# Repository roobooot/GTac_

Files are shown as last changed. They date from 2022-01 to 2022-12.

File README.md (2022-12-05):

# A Biomimetic Design of HeteroGeneous Tactile Sensor (GTac) Providing Normal and Shear Force Feedback

## General Introduction

This repo includes:

<ul>
  <li>the <a href="https://github.com/roobooot/GTac_/tree/main/software">code</a> 
    <ul>
      <li><a href="https://github.com/roobooot/GTac_/tree/main/software/arduino_lib">low-level controller</a> of GTac-Hand and GTac-Gripper</li>
      <li><a href="https://github.com/roobooot/GTac_/tree/main/software/GTac_Sensor">collecting data from GTac</a></li>
      <li>algorithms used for case study in papers, for instance, learning-based ECS recognition, handover controller, force-closed grasping, etc.</li>
    </ul>
</li>
  <li>the <a href="https://github.com/roobooot/GTac_/tree/main/hardware">hardware design</a>.
    <ul>
      <li><a href="https://github.com/roobooot/GTac_/tree/main/hardware/PCB%20design">PCB design</a> of GTac, reading-out boards, and the motors driving boards.</li>
      <li><a href="https://github.com/roobooot/GTac_/tree/main/hardware/Mechanical%20design">mechenical design</a> (CAD models)</li>
    </ul>
    </li>
</ul>

## Published Works

### GTac: A Biomimetic Tactile Sensor with Skin-like Heterogeneous Force Feedback for Robots

This paper is to introduce the design, fabrication methods, and force sensing principles of GTac.
For more information, please check out our paper below.

<p align="center">
  
</p>

Z. Lu, X. Gao and H. Yu, "GTac: A Biomimetic Tactile Sensor With Skin-Like Heterogeneous Force Feedback for Robots," in IEEE Sensors Journal, vol. 22, no. 14, pp. 14491-14500, 15 July15, 2022, doi: 10.1109/JSEN.2022.3181128.

#### Video
<!---[![IMAGE ALT TEXT HERE](http://img.youtube.com/vi/Pmd8PvLpeUA/0.jpg)](https://youtu.be/Pmd8PvLpeUA)--->
<p align="center">
<a href="https://youtu.be/Pmd8PvLpeUA">
  GTac
</a>
</p>

## Contact Information
If you have any queries, do not hesitate to contact <a href="https://roobooot.github.io/">Zeyu Lu</a> (email: zeyu.lu@u.nus.edu).

## Acknowledge
This project is supervised by <a href="https://www.eng.nus.edu.sg/bme/staff/dr-yuhy/">Prof. Haoyong Yu</a> in <a href="https://wiki.nus.edu.sg/display/biorobotics/Biorobotics+Lab">Biorobotics Lab</a> @NUS.

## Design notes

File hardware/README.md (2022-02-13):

# Mechanical design
-Uncompress the zip

-open the hand_42_with_actua_box_v2.SLDASM in **Solidworks**. The design of GTac, and its integration can be found in the CAD model.
# PCB design
Using **EAGLE** to check out all the PCB design used to realize the GTac tactile sensing.

Image of sensing PCB:

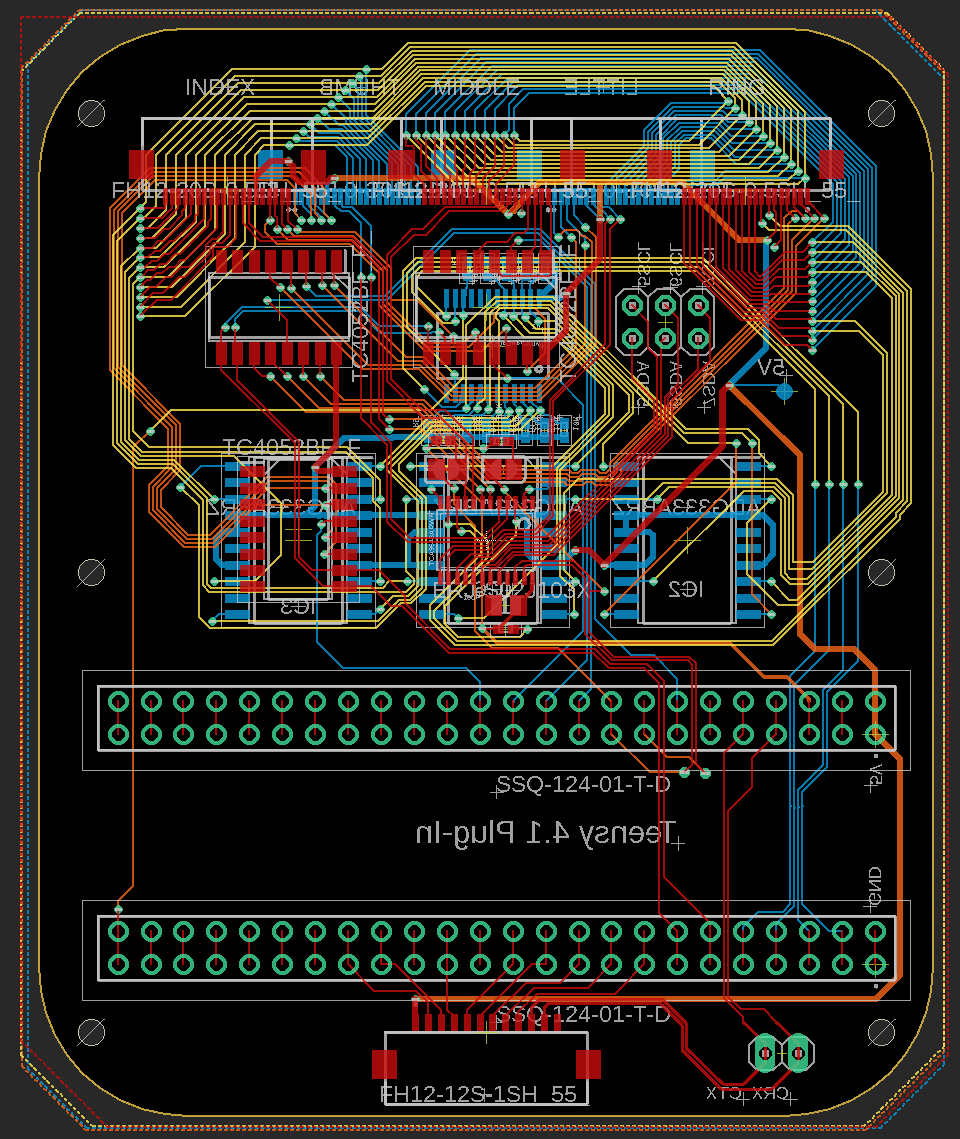
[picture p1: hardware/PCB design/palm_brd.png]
sensing PCB


Image of driving PCB:

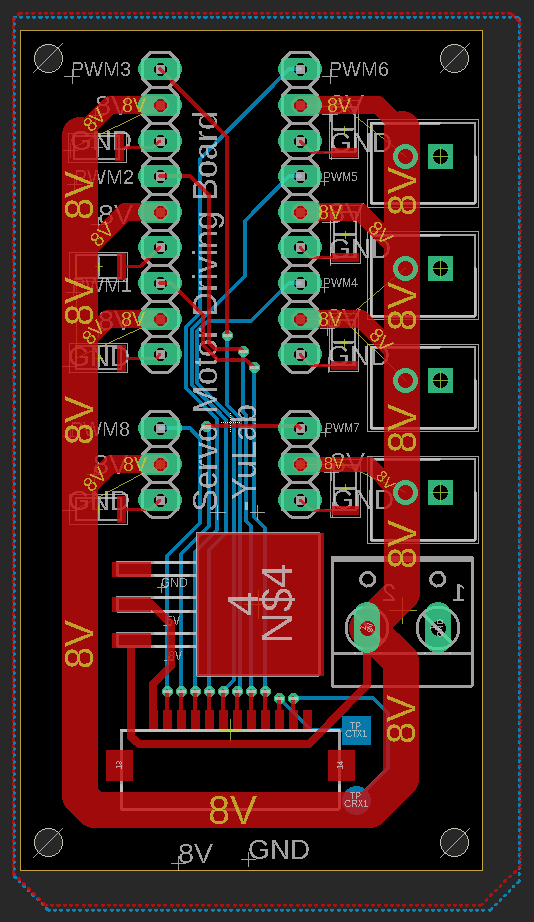
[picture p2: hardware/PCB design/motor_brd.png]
motor PCB


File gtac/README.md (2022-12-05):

# Python Interface for GTac Sensor

## Installation

Assuming your current directory is `GTac_/gtac/`, simply run
``` python
pip install .
```

To install for development, using `-e` option: `pip install -e .[dev]`

## Getting started

The main interface is `GtacInterface`. 
``` python
import gtac 

gtac_sensor = gtac.GtacInterface(serial_port="/dev/ttyACM0", data_index=6)
gtac_sensor.start()  # start the sensor
print(gtac_sensor.force)  # return a 3-dimensional numpy array 
print(gtac_sensor.pressure)  # return a 4-by-4 numpy array 
gtac_sensor.stop()  # stop the sensor
```

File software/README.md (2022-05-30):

## Minimum Requirement

### Environment Requirement
```
-Python3.6

-seaborn

-pandas

-tensorflow

-sklearn
```
### System Requirement
```
-Linus (Ubuntu 18.04 tested)
-Serial Port
```
## Quick setup
Set  ```/software/``` as the root path of the project to run the code inside.
### Serial port in Ubuntu
```ruby
//check serial port ID
dmesg
```
or
```ruby
sudo chmod 666 /dev/ttys0 
```
serial port ID in Windows example
```ruby
sudo chmod 666 /dev/ttyACM0 
```
serial port ID in Ubuntu example
### GTac sensor ID for readout board
```
f: 0,1,2,3,4 (thumb, index, middle, ring, little)
s: 0,1,2 (proximal, middle, distal)
```
### Real-time GTac feedback display
go to
```
software/GTac_Hand/
```
For instance, if the serial port is ```/dev/ttyACM0```, the GTac signals can be visualized by the following command
```ruby
python draw_line3.py -f 0 -s 0 -sp /dev/ttyACM0
```
or
```ruby
python draw_lines3_tosave_local.py -f 2 -s 0 -fn data/case_study/test_sensor_300_GTAC_Gripper20220420_172845.csv -l 0 -r test -sp /dev/ttyACM0
```
```
-f: sensor ID f
-s: sensor ID s
-l: 1 = local display; 0 = live display
-r: remarks for fileanmes of video to be saved
-sp: serial port ID
-fn: filename of data to be displayed
```
### Save GTac data
go to
```
software/GTac_Hand/
```
```ruby
python GTac_sensor.py -s 1 -d 300 -r test_sensor -sp /dev/ttyACM0
```
```
-s: 0 = not to save data; 1 = to save data
-d: number of datapoint (cycles) to save
-r: remarks of filename of data
-sp: serial port ID
```
```
default save path: data/
go to line-49 in GTac_sensor.py to change the save path.
```
### Use the saved GTac data
The saved GTac data has 293 columns. 
```
[285 + 6 + 1 + 1]
[GTac data + Serve motor angles * 6 + readout frequency + timeframe (ms)]
```
From left to the right, there are 285 GTac data signals when using the readout board that can produce digital signals for up to 15 GTac sensors. If less than 15 GTac sensors are used, only the related columns are with effective signals. 
#### GTac ID
Each used GTac sensor has a ID which is related to the hardware connection, which are 'finger' and 'sec'. 'finger' is [0,1,2,3,4] corresponding to the ports (thumb, index, middle, ring, little) that the sensors are connected to on the readout borad. Up to three GTac sensors can be serially connected to the each port of the readout board. Therefore, 'sec' is [0,1,2] which depends on the GTac sensors connected serially in each port, e.g., 'sec' is 0 if only one GTac sensor is used. 
#### GTac API 
##### Finding the signals in the 285 columns of GTac data
There are 19 signals for each GTac sensor which consists of 16 FA-I signals (4x4 arrayed normal force sensing) and 3 SA-II signals (global 3D contact forces in x, y, and z axis). Use the following functions to find the signals in demand.

###### Find the GTac signals:
FA-I:
https://github.com/roobooot/GTac_/blob/88ff11a90103c957f8382d993401048128073cff/software/GTac_Hand/GTac_Data.py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
SA-II:
https://github.com/roobooot/GTac_/blob/88ff11a90103c957f8382d993401048128073cff/software/GTac_Hand/GTac_Data.py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

###### Find the index in 285 GTac data:
FA-I:
https://github.com/roobooot/GTac_/blob/88ff11a90103c957f8382d993401048128073cff/software/GTac_Hand/GTac_Data.py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
SA-II:
https://github.com/roobooot/GTac_/blob/88ff11a90103c957f8382d993401048128073cff/software/GTac_Hand/GTac_Data.py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
SA-II:
All the 19 index for each GTac:
https://github.com/roobooot/GTac_/blob/88ff11a90103c957f8382d993401048128073cff/software/GTac_Hand/GTac_Data.py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

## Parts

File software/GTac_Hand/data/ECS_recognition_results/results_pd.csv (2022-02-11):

 | Value | Model | SWF | Metrics | Error | SWF_bi
0 | 0.023967726156115532 | CNN | w/o SWF | Loss | 0.9760322738438845 | 0
1 | 0.019740769639611244 | CNN | w/o SWF | Loss | 0.9802592303603888 | 0
2 | 0.021708421409130096 | CNN | w/o SWF | Loss | 0.9782915785908699 | 0
3 | 0.024480994790792465 | CNN | w/o SWF | Loss | 0.9755190052092075 | 0
4 | 0.021250680088996887 | CNN | w/o SWF | Loss | 0.9787493199110031 | 0
5 | 0.9936591160444993 | CNN | w/o SWF | Precision | 0.006340883955500698 | 0
6 | 0.9949290966558656 | CNN | w/o SWF | Precision | 0.005070903344134403 | 0
7 | 0.9942904934318557 | CNN | w/o SWF | Precision | 0.005709506568144285 | 0
8 | 0.9931152694339274 | CNN | w/o SWF | Precision | 0.006884730566072639 | 0
9 | 0.9940634415988007 | CNN | w/o SWF | Precision | 0.005936558401199332 | 0
10 | 0.9935897435897436 | CNN | w/o SWF | Recall | 0.0064102564102563875 | 0
11 | 0.9948717948717949 | CNN | w/o SWF | Recall | 0.00512820512820511 | 0
12 | 0.9942307692307693 | CNN | w/o SWF | Recall | 0.005769230769230749 | 0
13 | 0.9930341880341881 | CNN | w/o SWF | Recall | 0.006965811965811919 | 0
14 | 0.9939957264957265 | CNN | w/o SWF | Recall | 0.006004273504273461 | 0
15 | 0.9935897588729858 | CNN | w/o SWF | Accuracy | 0.00641024112701416 | 0
16 | 0.9948717951774597 | CNN | w/o SWF | Accuracy | 0.005128204822540283 | 0
17 | 0.9942307472229004 | CNN | w/o SWF | Accuracy | 0.005769252777099609 | 0
18 | 0.9930341839790344 | CNN | w/o SWF | Accuracy | 0.006965816020965576 | 0
19 | 0.993995726108551 | CNN | w/o SWF | Accuracy | 0.006004273891448975 | 0
20 | 0.014294200576841831 | CNN | w/ SWF | Loss | 0.9857057994231582 | 1
21 | 0.014593178406357765 | CNN | w/ SWF | Loss | 0.9854068215936422 | 1
22 | 0.01266512367874384 | CNN | w/ SWF | Loss | 0.9873348763212562 | 1
23 | 0.01688717119395733 | CNN | w/ SWF | Loss | 0.9831128288060427 | 1
24 | 0.015594863332808018 | CNN | w/ SWF | Loss | 0.984405136667192 | 1
25 | 0.9961288430813805 | CNN | w/ SWF | Precision | 0.0038711569186195005 | 1
26 | 0.9963602266992234 | CNN | w/ SWF | Precision | 0.003639773300776583 | 1
27 | 0.9964730624768824 | CNN | w/ SWF | Precision | 0.0035269375231176125 | 1
28 | 0.9952728899552802 | CNN | w/ SWF | Precision | 0.004727110044719818 | 1
29 | 0.9955819516839505 | CNN | w/ SWF | Precision | 0.004418048316049528 | 1
30 | 0.9960897435897436 | CNN | w/ SWF | Recall | 0.003910256410256441 | 1
31 | 0.9963461538461539 | CNN | w/ SWF | Recall | 0.0036538461538461187 | 1
32 | 0.9964529914529915 | CNN | w/ SWF | Recall | 0.003547008547008512 | 1
33 | 0.9952136752136752 | CNN | w/ SWF | Recall | 0.0047863247863247915 | 1
34 | 0.995534188034188 | CNN | w/ SWF | Recall | 0.004465811965811972 | 1
35 | 0.9960897564888 | CNN | w/ SWF | Accuracy | 0.003910243511199951 | 1
36 | 0.9963461756706238 | CNN | w/ SWF | Accuracy | 0.0036538243293762207 | 1
37 | 0.9964529871940613 | CNN | w/ SWF | Accuracy | 0.0035470128059387207 | 1
38 | 0.9952136874198914 | CNN | w/ SWF | Accuracy | 0.004786312580108643 | 1
39 | 0.9955341815948486 | CNN | w/ SWF | Accuracy | 0.004465818405151367 | 1
40 | 0.9104217727744365 | QDA | w/o SWF | Precision | 0.08957822722556352 | 0
41 | 0.9137111658410648 | QDA | w/o SWF | Precision | 0.08628883415893518 | 0
42 | 0.9098126192355684 | QDA | w/o SWF | Precision | 0.09018738076443156 | 0
43 | 0.9110353081376062 | QDA | w/o SWF | Precision | 0.08896469186239375 | 0
44 | 0.9116122928184544 | QDA | w/o SWF | Precision | 0.08838770718154565 | 0
45 | 0.8069871794871795 | QDA | w/o SWF | Recall | 0.19301282051282054 | 0
46 | 0.8135256410256411 | QDA | w/o SWF | Recall | 0.18647435897435893 | 0
47 | 0.8118589743589744 | QDA | w/o SWF | Recall | 0.18814102564102564 | 0
48 | 0.8103632478632479 | QDA | w/o SWF | Recall | 0.18963675213675213 | 0
49 | 0.8085897435897436 | QDA | w/o SWF | Recall | 0.19141025641025644 | 0
50 | 0.8069871794871795 | QDA | w/o SWF | Accuracy | 0.19301282051282054 | 0
51 | 0.8135256410256411 | QDA | w/o SWF | Accuracy | 0.18647435897435893 | 0
52 | 0.8118589743589744 | QDA | w/o SWF | Accuracy | 0.18814102564102564 | 0
53 | 0.8103632478632479 | QDA | w/o SWF | Accuracy | 0.18963675213675213 | 0
54 | 0.8085897435897436 | QDA | w/o SWF | Accuracy | 0.19141025641025644 | 0
55 | 0.8715989844008991 | QDA | w/ SWF | Precision | 0.1284010155991009 | 1
56 | 0.8679503102865198 | QDA | w/ SWF | Precision | 0.1320496897134802 | 1
57 | 0.8713535087328184 | QDA | w/ SWF | Precision | 0.12864649126718164 | 1
58 | 0.8753179997507231 | QDA | w/ SWF | Precision | 0.12468200024927689 | 1
59 | 0.8706857128583491 | QDA | w/ SWF | Precision | 0.12931428714165094 | 1
60 | 0.8210897435897436 | QDA | w/ SWF | Recall | 0.17891025641025637 | 1
61 | 0.8171794871794872 | QDA | w/ SWF | Recall | 0.18282051282051281 | 1
62 | 0.8232264957264958 | QDA | w/ SWF | Recall | 0.17677350427350424 | 1
63 | 0.8316880341880342 | QDA | w/ SWF | Recall | 0.16831196581196584 | 1
64 | 0.8211752136752136 | QDA | w/ SWF | Recall | 0.17882478632478638 | 1
65 | 0.8210897435897436 | QDA | w/ SWF | Accuracy | 0.17891025641025637 | 1
66 | 0.8171794871794872 | QDA | w/ SWF | Accuracy | 0.18282051282051281 | 1
67 | 0.8232264957264958 | QDA | w/ SWF | Accuracy | 0.17677350427350424 | 1
68 | 0.8316880341880342 | QDA | w/ SWF | Accuracy | 0.16831196581196584 | 1
69 | 0.8211752136752136 | QDA | w/ SWF | Accuracy | 0.17882478632478638 | 1

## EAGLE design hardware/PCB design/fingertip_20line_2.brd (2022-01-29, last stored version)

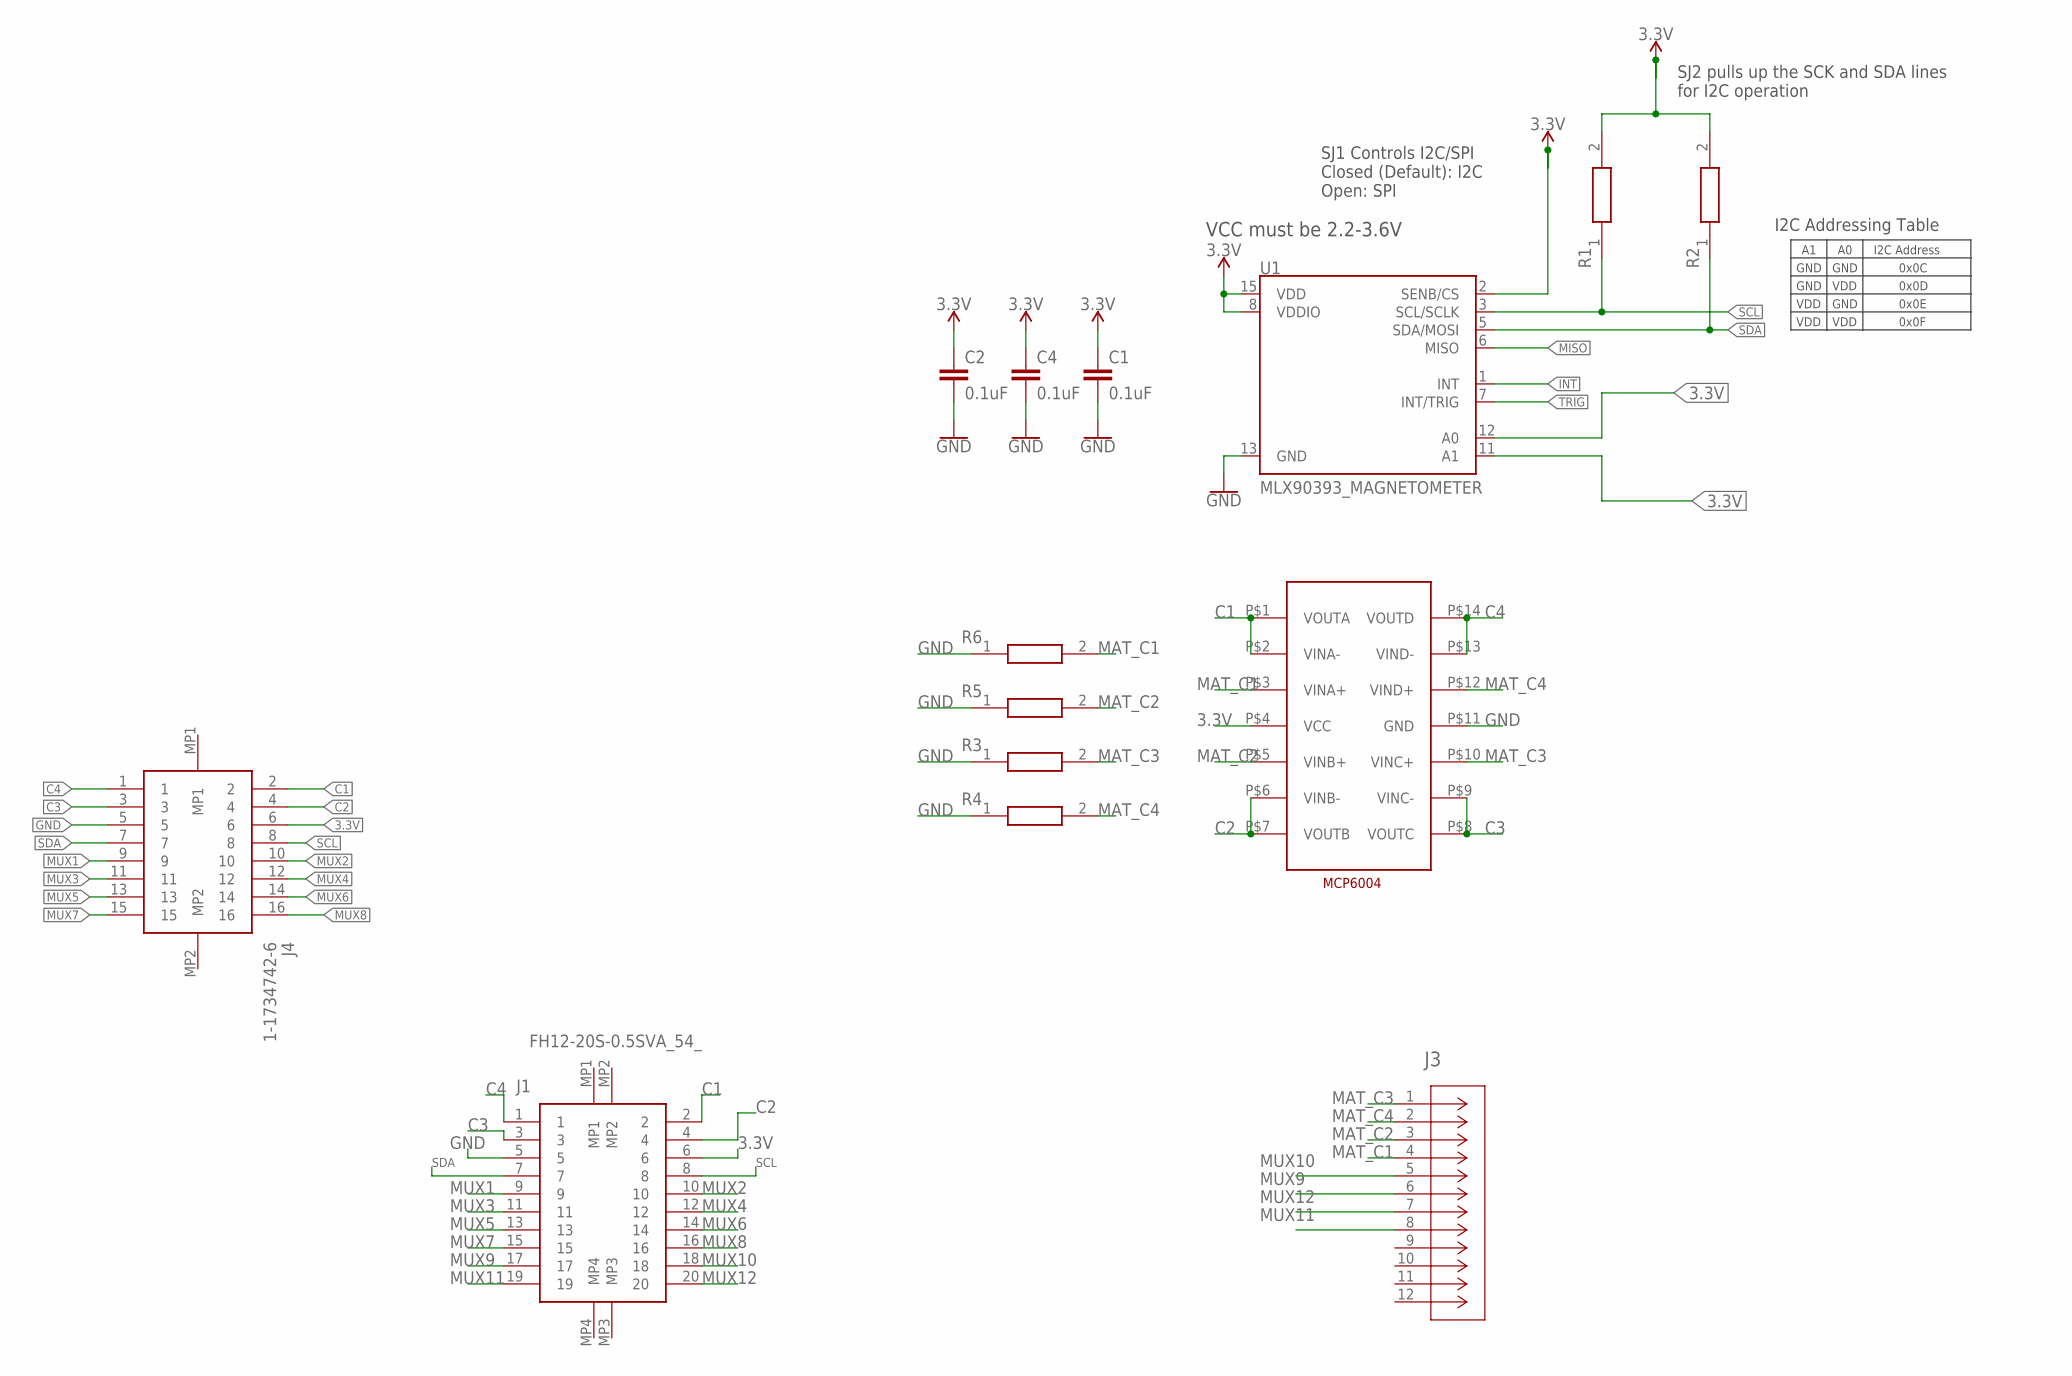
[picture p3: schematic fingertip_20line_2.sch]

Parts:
C1, C2, C4: 0.1uF; 0603
J1: FH12-20S-0.5SVA_54_; FH1220S05SVA54
J3: FH12-8S-1SV(55); CON8_1X8_DUTB1_HRS_HIR
J4: 1-1734742-6; 117347426
R1, R2, R3, R4, R5, R6: ERJ-S02J103X; RESC1005X40N
U1: MLX90393_MAGNETOMETER; QFN-16_WITH_AXIES
U$2: DECADE-MCP6004; DECADE-MCP6003

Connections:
3.3V: C1.1, C2.1, C4.1, J1.6, J4.6, R1.2, R2.2, U1.2 (SENB/CS), U1.8 (VDDIO), U1.11 (A1), U1.12 (A0), U1.15 (VDD), U$2.P$4 (VCC)
C1: J1.2, J4.2, U$2.P$1 (VOUTA), U$2.P$2 (VINA-)
C2: J1.4, J4.4, U$2.P$6 (VINB-), U$2.P$7 (VOUTB)
C3: J1.3, J4.3, U$2.P$8 (VOUTC), U$2.P$9 (VINC-)
C4: J1.1, J4.1, U$2.P$13 (VIND-), U$2.P$14 (VOUTD)
GND: C1.2, C2.2, C4.2, J1.5, J4.5, R3.1, R4.1, R5.1, R6.1, U1.13 (GND), U$2.P$11 (GND)
INT: U1.1 (INT)
MAT_C1: J3.4, R6.2, U$2.P$3 (VINA+)
MAT_C2: J3.3, R5.2, U$2.P$5 (VINB+)
MAT_C3: J3.1, R3.2, U$2.P$10 (VINC+)
MAT_C4: J3.2, R4.2, U$2.P$12 (VIND+)
MISO: U1.6 (MISO)
MUX1: J1.9, J4.9
MUX2: J1.10, J4.10
MUX3: J1.11, J4.11
MUX4: J1.12, J4.12
MUX5: J1.13, J4.13
MUX6: J1.14, J4.14
MUX7: J1.15, J4.15
MUX8: J1.16, J4.16
MUX9: J1.17, J3.6
MUX10: J1.18, J3.5
MUX11: J1.19, J3.8
MUX12: J1.20, J3.7
SCL: J1.8, J4.8, R1.1, U1.3 (SCL/SCLK)
SDA: J1.7, J4.7, R2.1, U1.5 (SDA/MOSI)
TRIG: U1.7 (INT/TRIG)

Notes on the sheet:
SJ2 pulls up the SCK and SDA lines for I2C operation
VCC must be 2.2-3.6V
SJ1 Controls I2C/SPI Closed (Default): I2C Open: SPI
I2C Address
0x0C
0x0D
0x0E
0x0F
GND
VDD
I2C Addressing Table

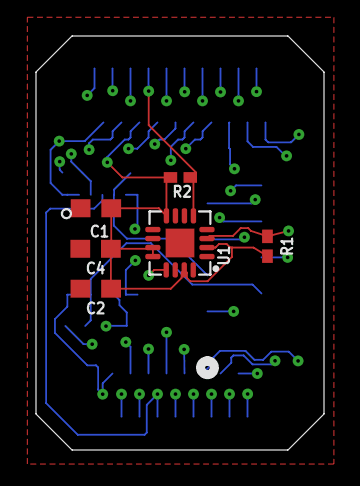
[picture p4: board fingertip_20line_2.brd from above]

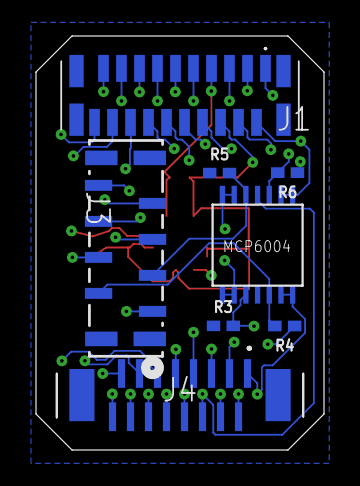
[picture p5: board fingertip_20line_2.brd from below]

Board: 4 copper layers, 16.0 x 23.0 mm, 14 parts (8 on the bottom side), 24 nets.

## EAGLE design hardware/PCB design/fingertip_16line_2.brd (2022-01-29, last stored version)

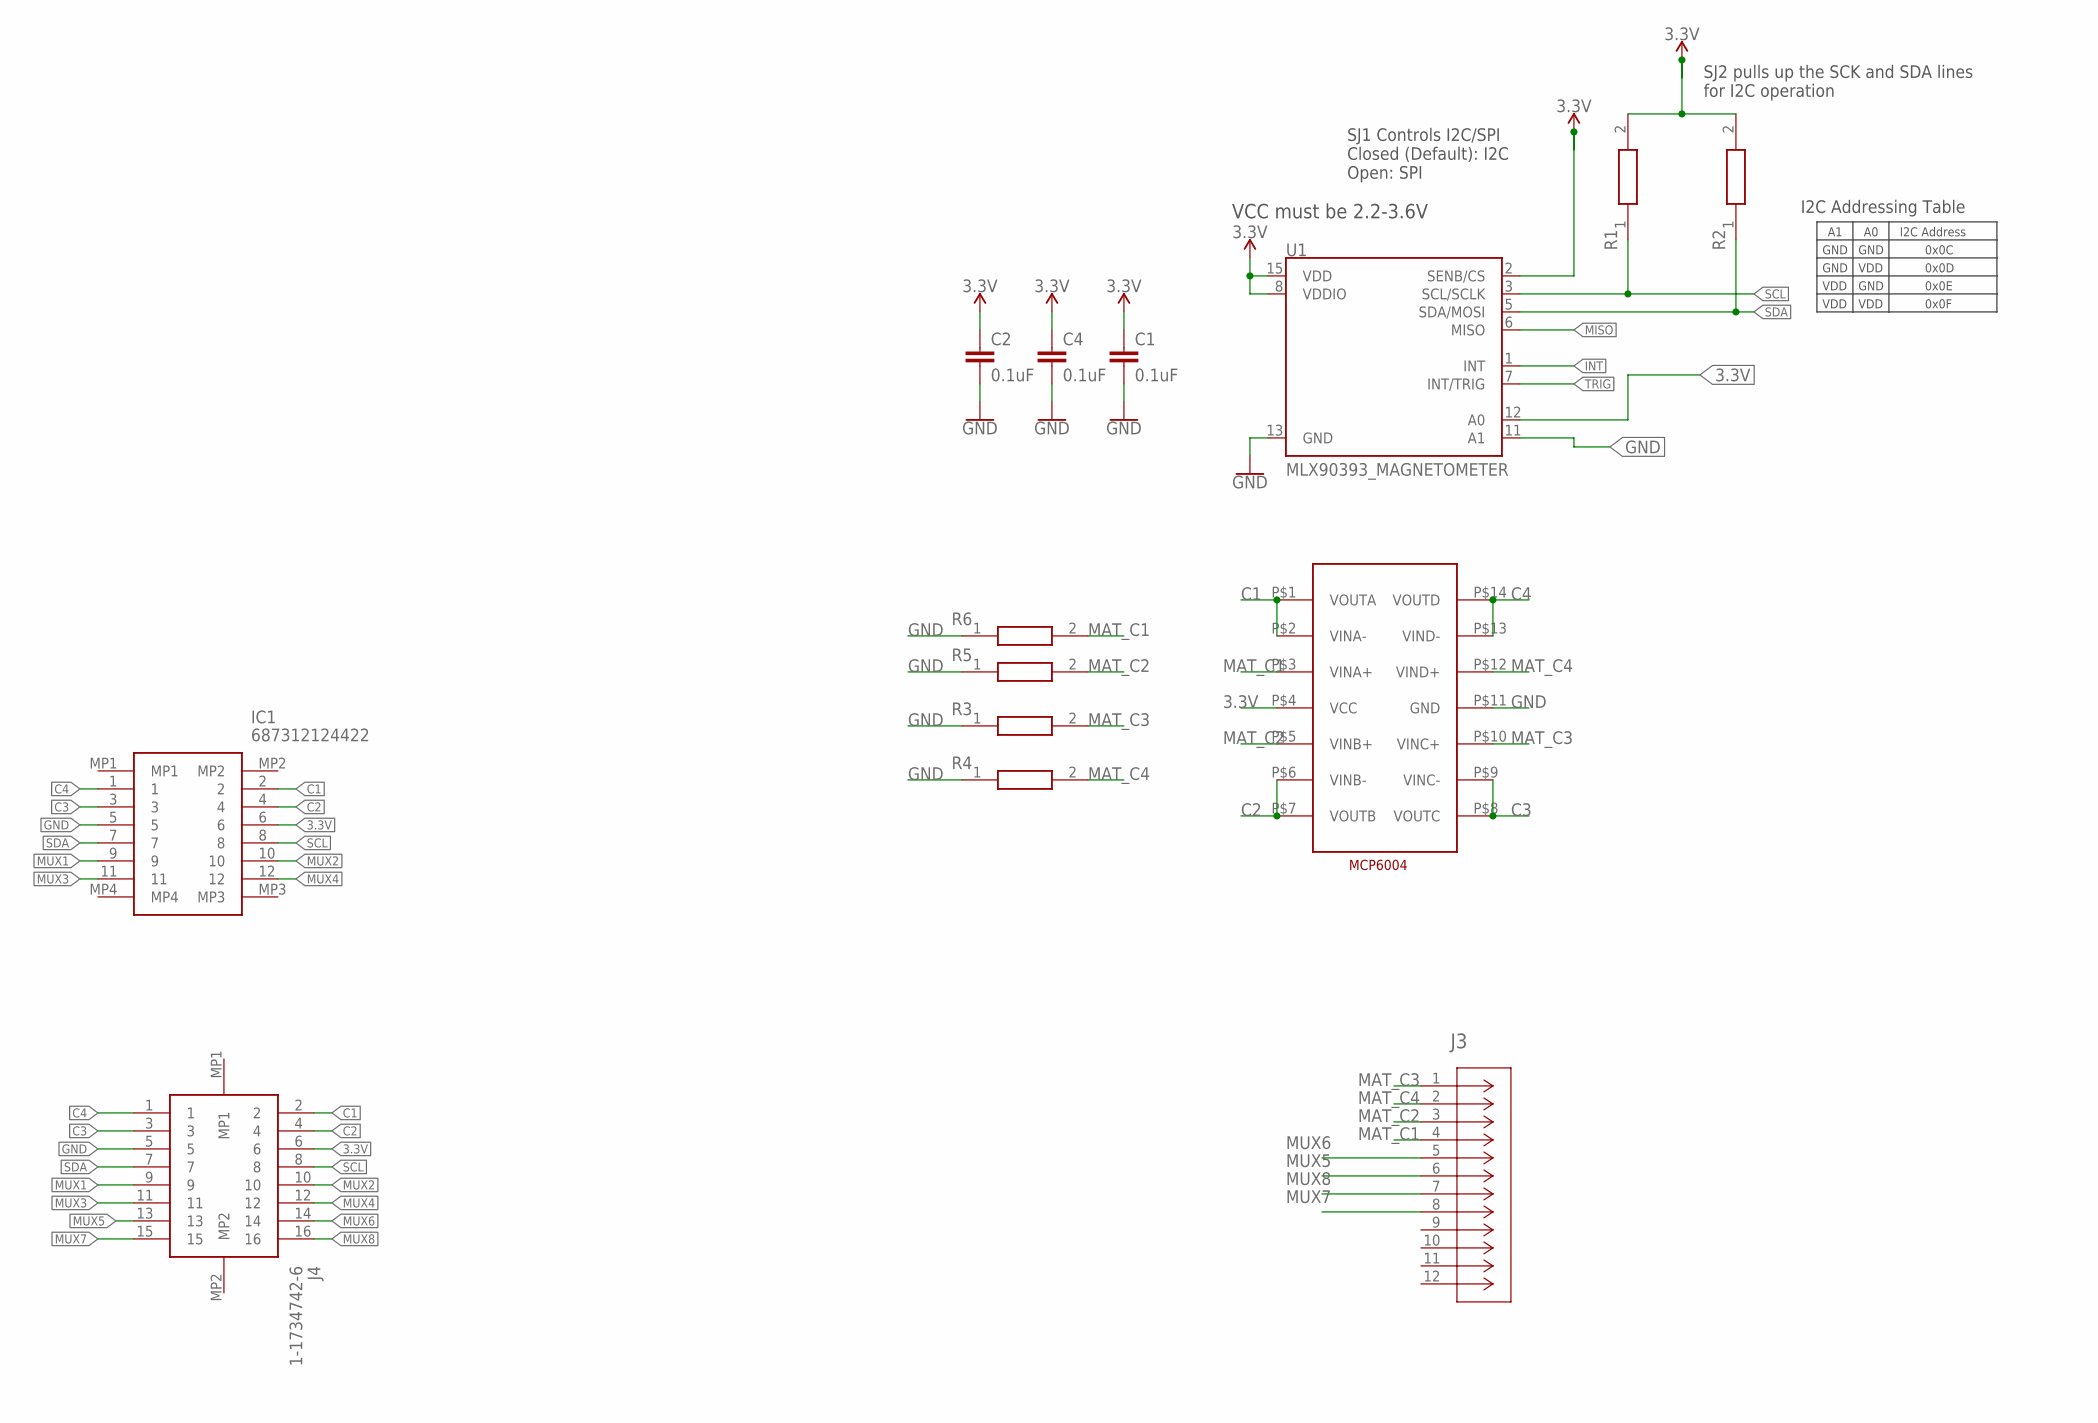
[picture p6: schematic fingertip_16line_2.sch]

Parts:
C1, C2, C4: 0.1uF; 0402
IC1: 687312124422
J3: FH12-8S-1SV(55); CON8_1X8_DUTB1_HRS_HIR
J4: 1-1734742-6; 117347426
R1, R2, R3, R4, R5, R6: ERJ-S02J103X; RESC1005X40N
U1: MLX90393_MAGNETOMETER; QFN-16_WITH_AXIES
U$2: DECADE-MCP6004; DECADE-MCP6003

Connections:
3.3V: C1.1, C2.1, C4.1, IC1.6, J4.6, R1.2, R2.2, U1.2 (SENB/CS), U1.8 (VDDIO), U1.12 (A0), U1.15 (VDD), U$2.P$4 (VCC)
C1: IC1.2, J4.2, U$2.P$1 (VOUTA), U$2.P$2 (VINA-)
C2: IC1.4, J4.4, U$2.P$6 (VINB-), U$2.P$7 (VOUTB)
C3: IC1.3, J4.3, U$2.P$8 (VOUTC), U$2.P$9 (VINC-)
C4: IC1.1, J4.1, U$2.P$13 (VIND-), U$2.P$14 (VOUTD)
GND: C1.2, C2.2, C4.2, IC1.5, J4.5, R3.1, R4.1, R5.1, R6.1, U1.11 (A1), U1.13 (GND), U$2.P$11 (GND)
INT: U1.1 (INT)
MAT_C1: J3.4, R6.2, U$2.P$3 (VINA+)
MAT_C2: J3.3, R5.2, U$2.P$5 (VINB+)
MAT_C3: J3.1, R3.2, U$2.P$10 (VINC+)
MAT_C4: J3.2, R4.2, U$2.P$12 (VIND+)
MISO: U1.6 (MISO)
MUX1: IC1.9, J4.9
MUX2: IC1.10, J4.10
MUX3: IC1.11, J4.11
MUX4: IC1.12, J4.12
MUX5: J3.6, J4.13
MUX6: J3.5, J4.14
MUX7: J3.8, J4.15
MUX8: J3.7, J4.16
SCL: IC1.8, J4.8, R1.1, U1.3 (SCL/SCLK)
SDA: IC1.7, J4.7, R2.1, U1.5 (SDA/MOSI)
TRIG: U1.7 (INT/TRIG)

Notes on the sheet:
SJ2 pulls up the SCK and SDA lines for I2C operation
VCC must be 2.2-3.6V
SJ1 Controls I2C/SPI Closed (Default): I2C Open: SPI
I2C Address
0x0C
0x0D
0x0E
0x0F
GND
VDD
I2C Addressing Table

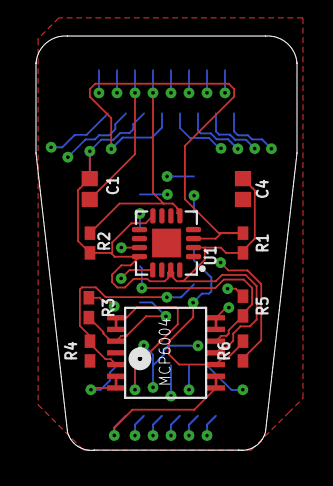
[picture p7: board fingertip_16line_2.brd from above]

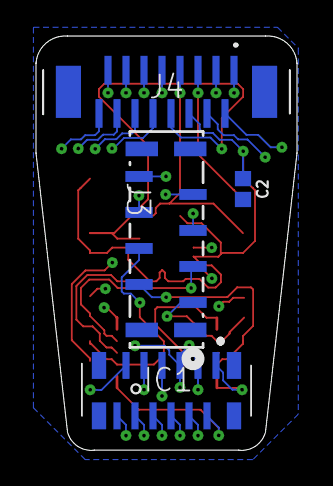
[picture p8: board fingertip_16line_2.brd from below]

Board: 4 copper layers, 14.5 x 23.0 mm, 14 parts (4 on the bottom side), 20 nets.

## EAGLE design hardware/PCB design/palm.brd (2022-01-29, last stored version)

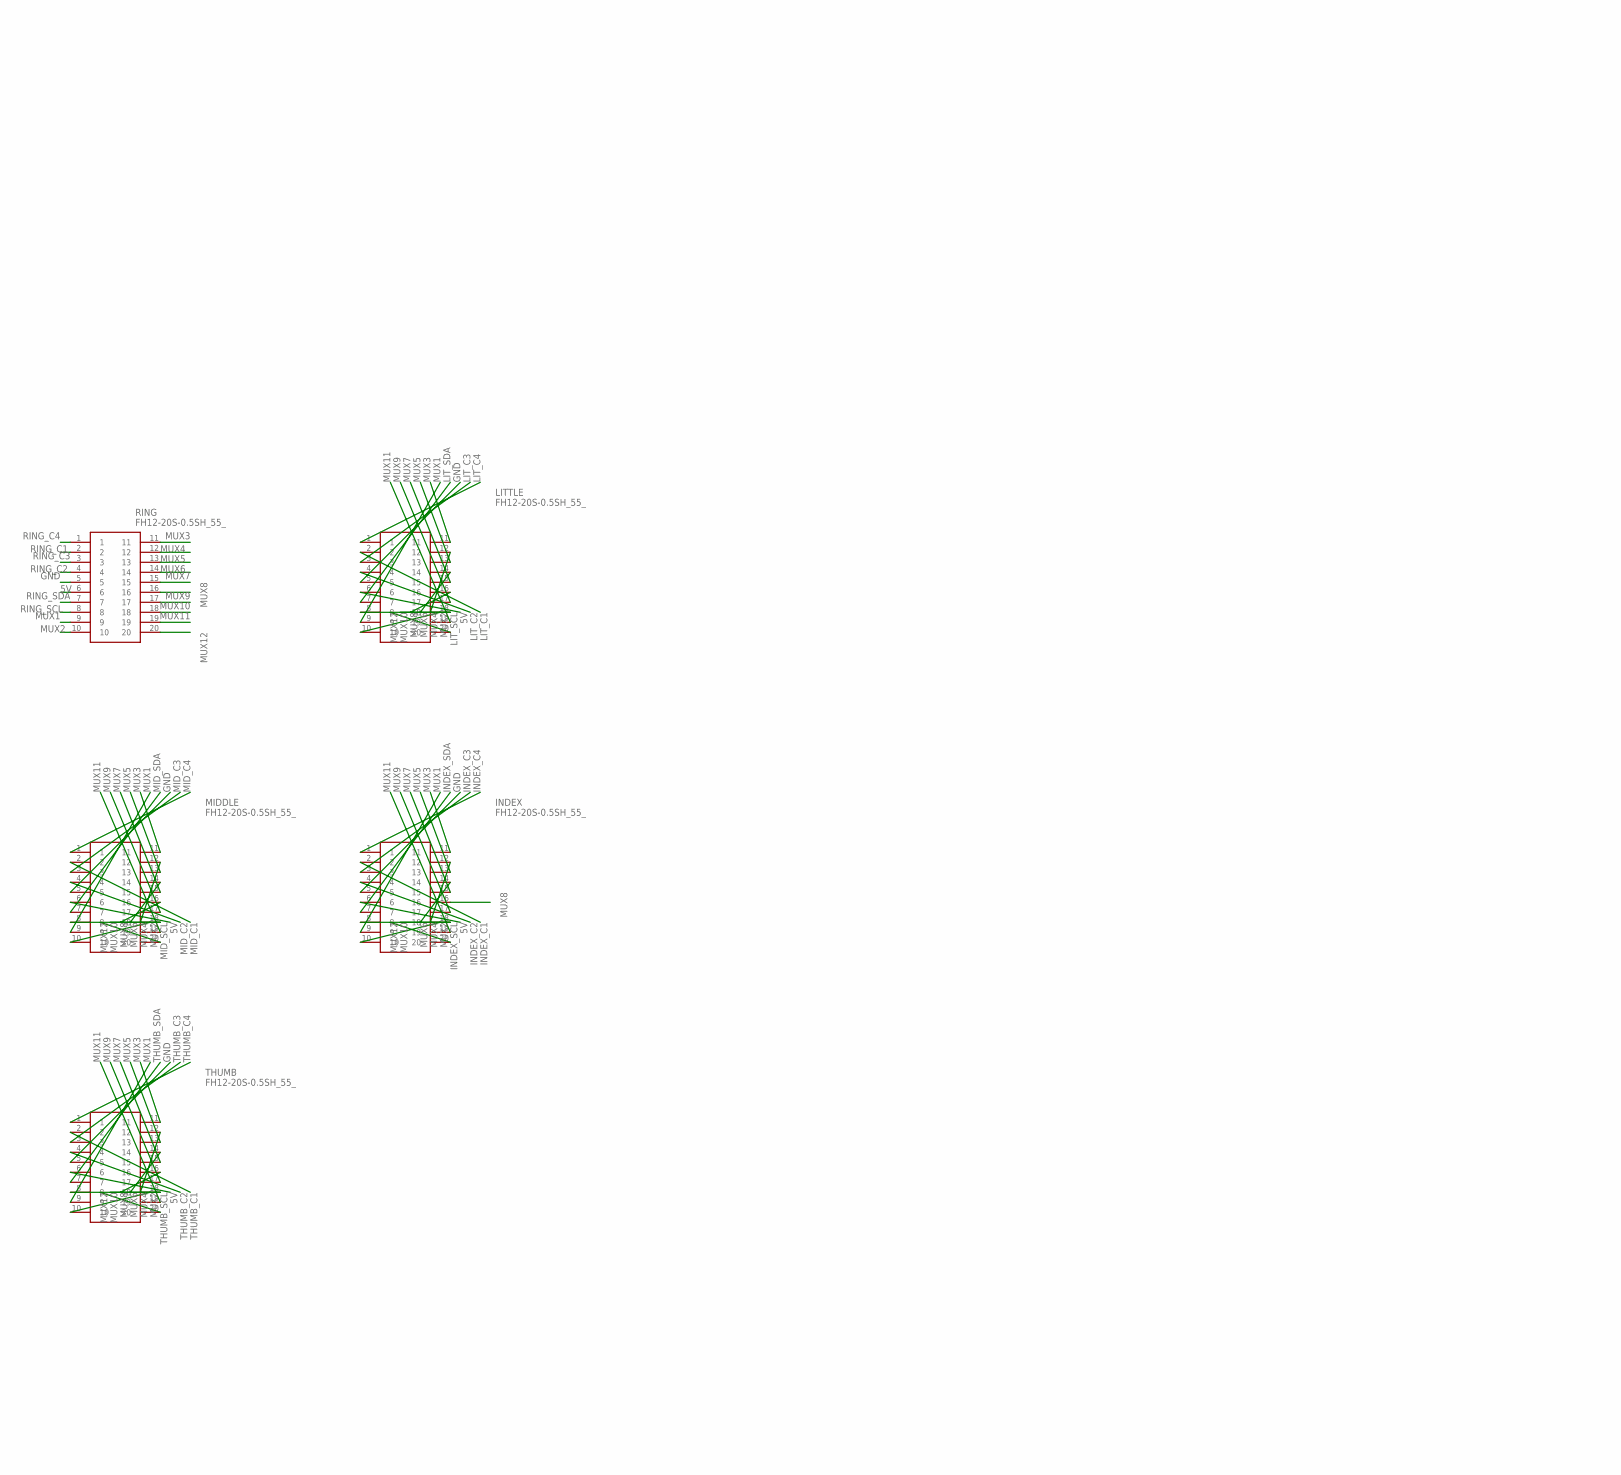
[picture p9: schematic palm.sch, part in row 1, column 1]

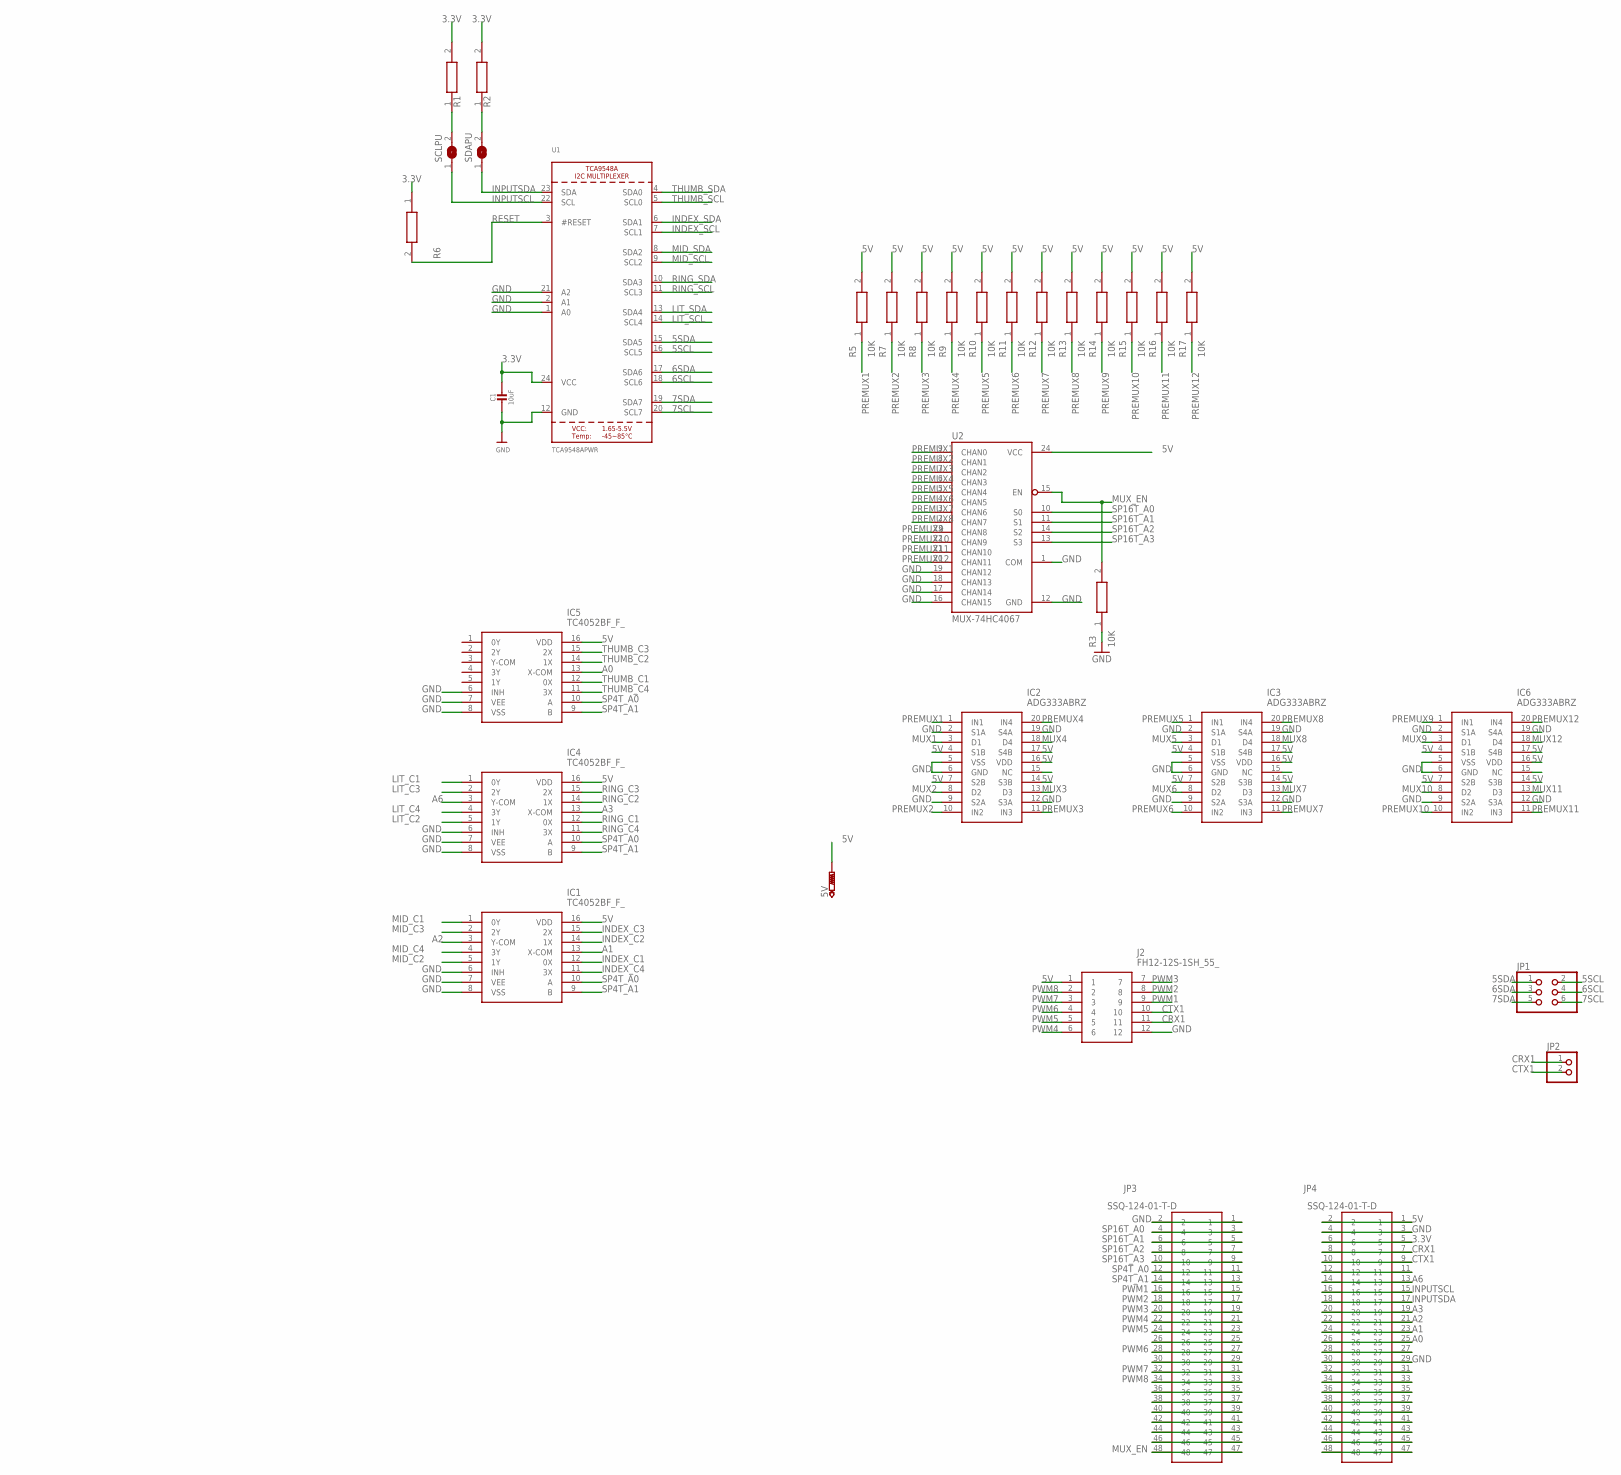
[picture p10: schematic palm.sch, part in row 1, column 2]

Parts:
5V: PTR1B1,27; B1,27
C1: 10uF; 0805-NO
IC1, IC4, IC5: TC4052BF_F_; SOIC127P780X190-16N
IC2, IC3, IC6: ADG333ABRZ; SOIC127P1032X265-20N
INDEX: FH12-20S-0.5SH_55_; FH12-20S-0.5SH(55)
J2: FH12-12S-1SH_55_; FH12-12S-1SH(55)
JP1: PINHD-2X3; 2X03
JP2: PINHD-1X2; 1X02
JP3, JP4: SSQ-124-01-T-D; SSQ-124-XX-YYY
LITTLE: FH12-20S-0.5SH_55_; FH12-20S-0.5SH(55)
MIDDLE: FH12-20S-0.5SH_55_; FH12-20S-0.5SH(55)
R1, R2, R6: ERJ-S02J103X; RESC1005X40N
R3, R5, R7, R8, R9, R10, R11, R12, R13, R14, R15, R16, R17: 10K; RESC1005X40N
RING: FH12-20S-0.5SH_55_; FH12-20S-0.5SH(55)
SCLPU: SOLDERJUMPERCLOSED; SOLDERJUMPER_CLOSEDWIRE
SDAPU: SOLDERJUMPERCLOSED; SOLDERJUMPER_CLOSEDWIRE
THUMB: FH12-20S-0.5SH_55_; FH12-20S-0.5SH(55)
U1: TCA9548APWR; TSSOP24
U2: MUX-74HC4067; SSOP24

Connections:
3.3V: C1.1, JP4.5, JP4.6, R1.2, R2.2, R6.1, U1.24 (VCC)
5SCL: JP1.2, U1.16 (SCL5)
5SDA: JP1.1, U1.15 (SDA5)
5V: 5V.TP, IC1.16 (VDD), IC2.4 (S1B), IC2.7 (S2B), IC2.14 (S3B), IC2.16 (VDD), IC2.17 (S4B), IC3.4 (S1B), IC3.7 (S2B), IC3.14 (S3B), IC3.16 (VDD), IC3.17 (S4B), IC4.16 (VDD), IC5.16 (VDD), IC6.4 (S1B), IC6.7 (S2B), IC6.14 (S3B), IC6.16 (VDD), IC6.17 (S4B), INDEX.6, J2.1, JP4.1, JP4.2, LITTLE.6, MIDDLE.6, R5.2, R7.2, R8.2, R9.2, R10.2, R11.2, R12.2, R13.2, R14.2, R15.2, R16.2, R17.2, RING.6, THUMB.6, U2.24 (VCC)
6SCL: JP1.4, U1.18 (SCL6)
6SDA: JP1.3, U1.17 (SDA6)
7SCL: JP1.6, U1.20 (SCL7)
7SDA: JP1.5, U1.19 (SDA7)
A0: IC5.13 (X-COM), JP4.25, JP4.26
A1: IC1.13 (X-COM), JP4.23, JP4.24
A2: IC1.3 (Y-COM), JP4.21, JP4.22
A3: IC4.13 (X-COM), JP4.19, JP4.20
A6: IC4.3 (Y-COM), JP4.13, JP4.14
CRX1: J2.11, JP2.1, JP4.7, JP4.8
CTX1: J2.10, JP2.2, JP4.9, JP4.10
GND: C1.2, IC1.6 (INH), IC1.7 (VEE), IC1.8 (VSS), IC2.2 (S1A), IC2.5 (VSS), IC2.6 (GND), IC2.9 (S2A), IC2.12 (S3A), IC2.19 (S4A), IC3.2 (S1A), IC3.5 (VSS), IC3.6 (GND), IC3.9 (S2A), IC3.12 (S3A), IC3.19 (S4A), IC4.6 (INH), IC4.7 (VEE), IC4.8 (VSS), IC5.6 (INH), IC5.7 (VEE), IC5.8 (VSS), IC6.2 (S1A), IC6.5 (VSS), IC6.6 (GND), IC6.9 (S2A), IC6.12 (S3A), IC6.19 (S4A), INDEX.5, J2.12, JP3.1, JP3.2, JP4.3, JP4.4, JP4.29, JP4.30, LITTLE.5, MIDDLE.5, R3.1, RING.5, THUMB.5, U1.1 (A0), U1.2 (A1), U1.12 (GND), U1.21 (A2), U2.1 (COM), U2.12 (GND), U2.16 (CHAN15), U2.17 (CHAN14), U2.18 (CHAN13), U2.19 (CHAN12)
INDEX_C1: IC1.12 (0X), INDEX.2
INDEX_C2: IC1.14 (1X), INDEX.4
INDEX_C3: IC1.15 (2X), INDEX.3
INDEX_C4: IC1.11 (3X), INDEX.1
INDEX_SCL: INDEX.8, U1.7 (SCL1)
INDEX_SDA: INDEX.7, U1.6 (SDA1)
INPUTSCL: JP4.15, JP4.16, SCLPU.1, U1.22 (SCL)
INPUTSDA: JP4.17, JP4.18, SDAPU.1, U1.23 (SDA)
LIT_C1: IC4.1 (0Y), LITTLE.2
LIT_C2: IC4.5 (1Y), LITTLE.4
LIT_C3: IC4.2 (2Y), LITTLE.3
LIT_C4: IC4.4 (3Y), LITTLE.1
LIT_SCL: LITTLE.8, U1.14 (SCL4)
LIT_SDA: LITTLE.7, U1.13 (SDA4)
MID_C1: IC1.1 (0Y), MIDDLE.2
MID_C2: IC1.5 (1Y), MIDDLE.4
MID_C3: IC1.2 (2Y), MIDDLE.3
MID_C4: IC1.4 (3Y), MIDDLE.1
MID_SCL: MIDDLE.8, U1.9 (SCL2)
MID_SDA: MIDDLE.7, U1.8 (SDA2)
MUX1: IC2.3 (D1), INDEX.9, LITTLE.9, MIDDLE.9, RING.9, THUMB.9
MUX2: IC2.8 (D2), INDEX.10, LITTLE.10, MIDDLE.10, RING.10, THUMB.10
MUX3: IC2.13 (D3), INDEX.11, LITTLE.11, MIDDLE.11, RING.11, THUMB.11
MUX4: IC2.18 (D4), INDEX.12, LITTLE.12, MIDDLE.12, RING.12, THUMB.12
MUX5: IC3.3 (D1), INDEX.13, LITTLE.13, MIDDLE.13, RING.13, THUMB.13
MUX6: IC3.8 (D2), INDEX.14, LITTLE.14, MIDDLE.14, RING.14, THUMB.14
MUX7: IC3.13 (D3), INDEX.15, LITTLE.15, MIDDLE.15, RING.15, THUMB.15
MUX8: IC3.18 (D4), INDEX.16, LITTLE.16, MIDDLE.16, RING.16, THUMB.16
MUX9: IC6.3 (D1), INDEX.17, LITTLE.17, MIDDLE.17, RING.17, THUMB.17
MUX10: IC6.8 (D2), INDEX.18, LITTLE.18, MIDDLE.18, RING.18, THUMB.18
MUX11: IC6.13 (D3), INDEX.19, LITTLE.19, MIDDLE.19, RING.19, THUMB.19
MUX12: IC6.18 (D4), INDEX.20, LITTLE.20, MIDDLE.20, RING.20, THUMB.20
MUX_EN: JP3.47, JP3.48, R3.2, U2.15 (EN)
unnamed: R1.1, SCLPU.2
unnamed: R2.1, SDAPU.2
unnamed: JP3.25, JP3.26
unnamed: JP3.29, JP3.30
unnamed: JP3.35, JP3.36
unnamed: JP3.37, JP3.38
unnamed: JP3.39, JP3.40
unnamed: JP3.41, JP3.42
unnamed: JP3.43, JP3.44
unnamed: JP3.45, JP3.46
unnamed: JP4.11, JP4.12
unnamed: JP4.27, JP4.28
unnamed: JP4.31, JP4.32
unnamed: JP4.33, JP4.34
unnamed: JP4.35, JP4.36
unnamed: JP4.37, JP4.38
unnamed: JP4.39, JP4.40
unnamed: JP4.41, JP4.42
unnamed: JP4.43, JP4.44
unnamed: JP4.45, JP4.46
unnamed: JP4.47, JP4.48
PREMUX1: IC2.1 (IN1), R5.1, U2.9 (CHAN0)
PREMUX2: IC2.10 (IN2), R7.1, U2.8 (CHAN1)
PREMUX3: IC2.11 (IN3), R8.1, U2.7 (CHAN2)
PREMUX4: IC2.20 (IN4), R9.1, U2.6 (CHAN3)
PREMUX5: IC3.1 (IN1), R10.1, U2.5 (CHAN4)
PREMUX6: IC3.10 (IN2), R11.1, U2.4 (CHAN5)
PREMUX7: IC3.11 (IN3), R12.1, U2.3 (CHAN6)
PREMUX8: IC3.20 (IN4), R13.1, U2.2 (CHAN7)
PREMUX9: IC6.1 (IN1), R14.1, U2.23 (CHAN8)
PREMUX10: IC6.10 (IN2), R15.1, U2.22 (CHAN9)
PREMUX11: IC6.11 (IN3), R16.1, U2.21 (CHAN10)
PREMUX12: IC6.20 (IN4), R17.1, U2.20 (CHAN11)
PWM1: J2.9, JP3.15, JP3.16
PWM2: J2.8, JP3.17, JP3.18
PWM3: J2.7, JP3.19, JP3.20
PWM4: J2.6, JP3.21, JP3.22
PWM5: J2.5, JP3.23, JP3.24
PWM6: J2.4, JP3.27, JP3.28
PWM7: J2.3, JP3.31, JP3.32
PWM8: J2.2, JP3.33, JP3.34
RESET: R6.2, U1.3 (#RESET)
RING_C1: IC4.12 (0X), RING.2
RING_C2: IC4.14 (1X), RING.4
RING_C3: IC4.15 (2X), RING.3
RING_C4: IC4.11 (3X), RING.1
RING_SCL: RING.8, U1.11 (SCL3)
RING_SDA: RING.7, U1.10 (SDA3)
SP4T_A0: IC1.10 (A), IC4.10 (A), IC5.10 (A), JP3.11, JP3.12
SP4T_A1: IC1.9 (B), IC4.9 (B), IC5.9 (B), JP3.13, JP3.14
SP16T_A0: JP3.3, JP3.4, U2.10 (S0)
SP16T_A1: JP3.5, JP3.6, U2.11 (S1)
SP16T_A2: JP3.7, JP3.8, U2.14 (S2)
SP16T_A3: JP3.9, JP3.10, U2.13 (S3)
THUMB_C1: IC5.12 (0X), THUMB.2
THUMB_C2: IC5.14 (1X), THUMB.4
THUMB_C3: IC5.15 (2X), THUMB.3
THUMB_C4: IC5.11 (3X), THUMB.1
THUMB_SCL: THUMB.8, U1.5 (SCL0)
THUMB_SDA: THUMB.7, U1.4 (SDA0)

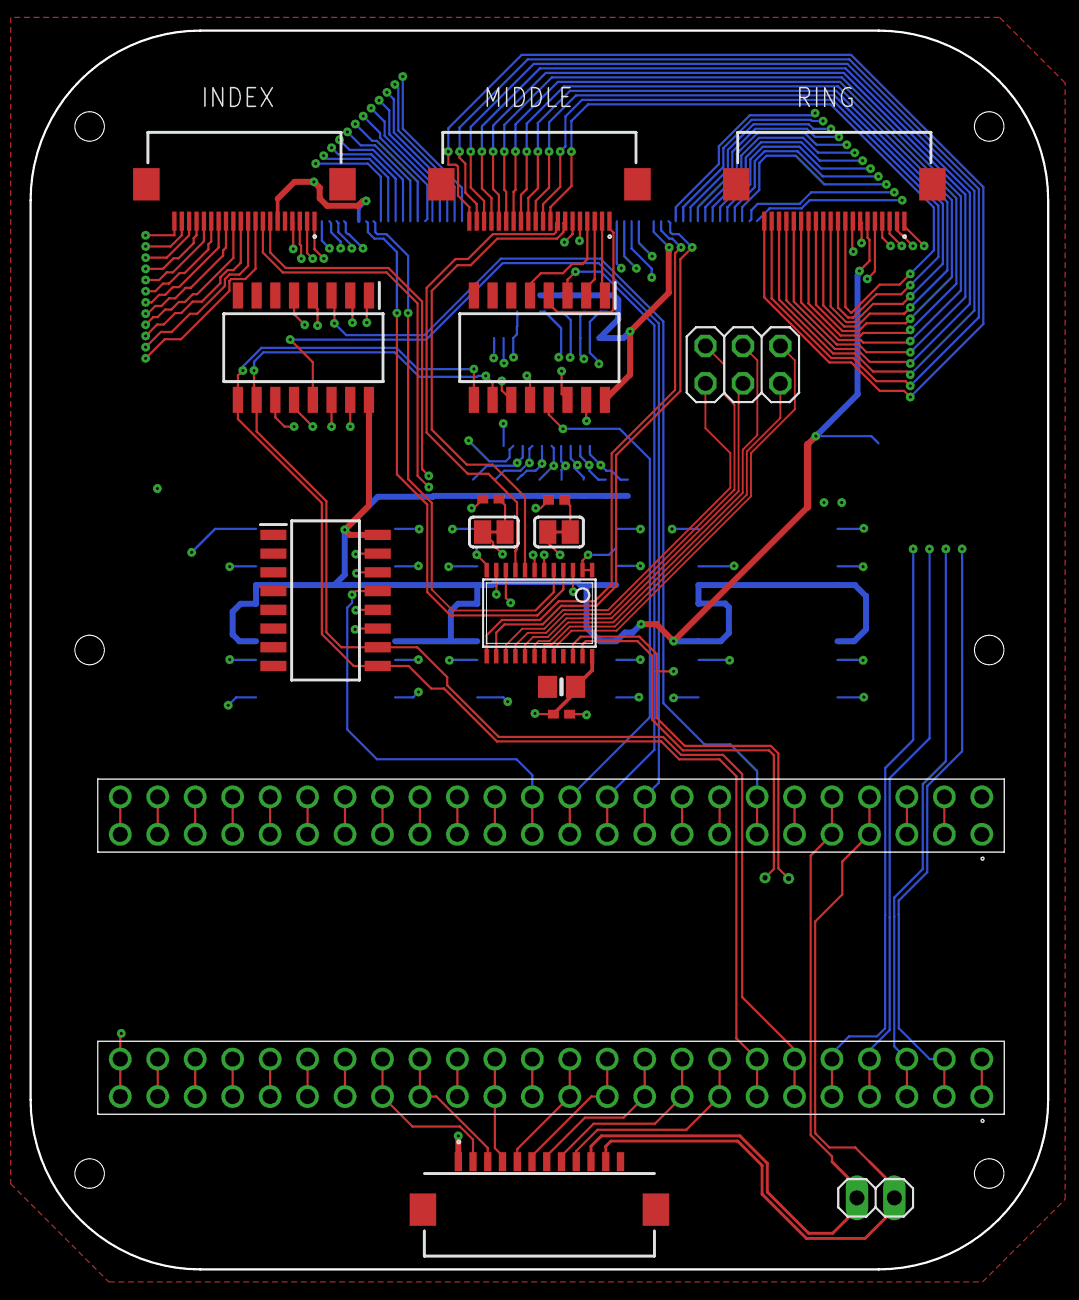
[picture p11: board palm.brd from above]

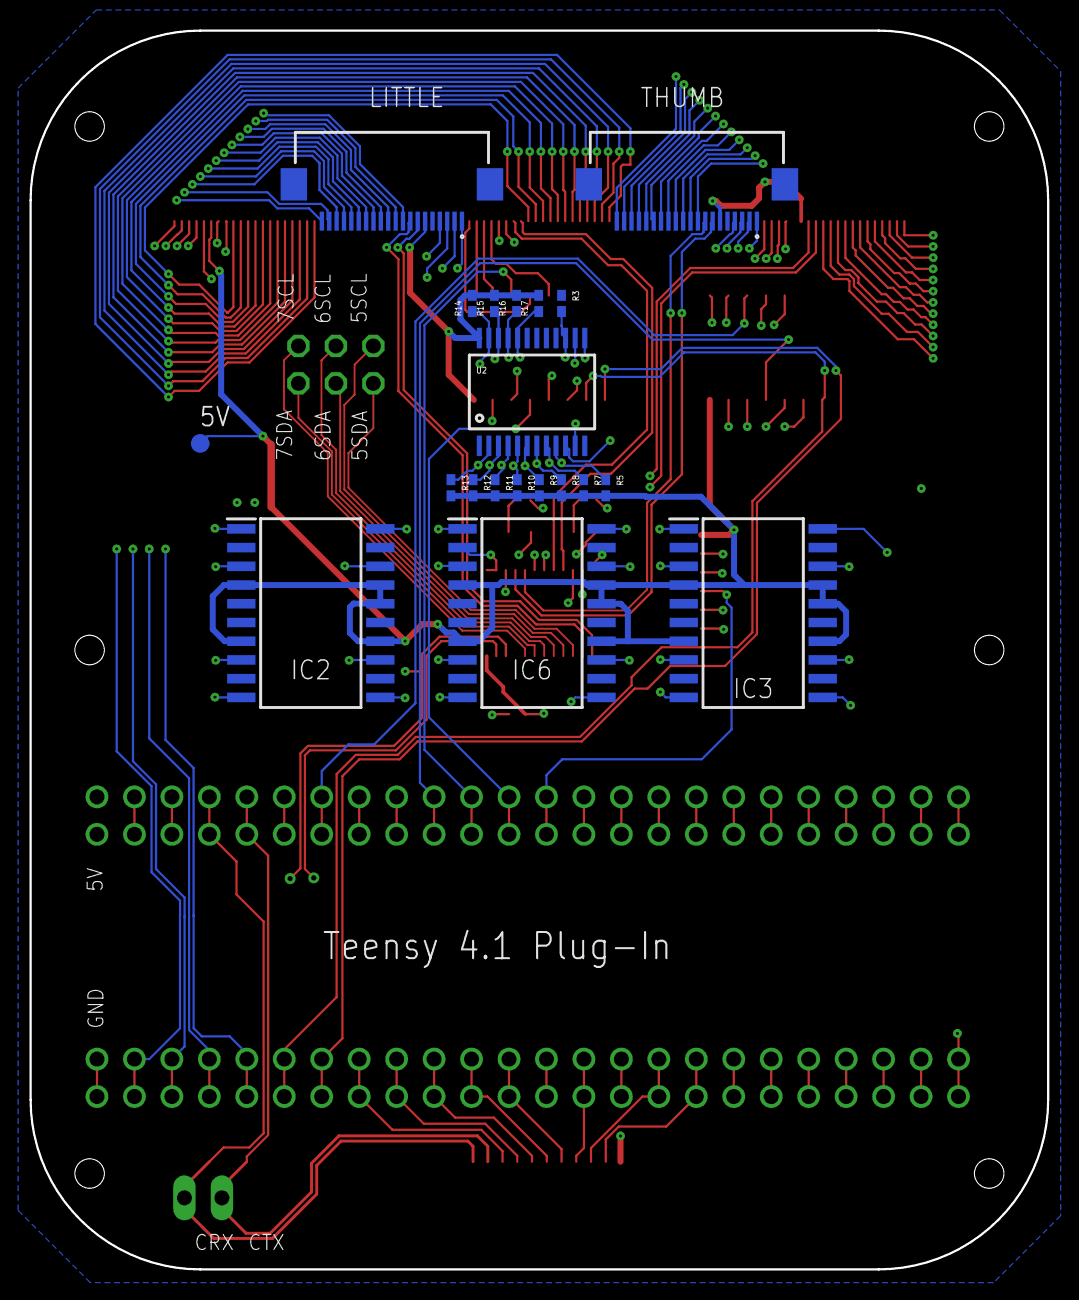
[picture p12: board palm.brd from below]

Board: 4 copper layers, 69.0 x 84.0 mm, 38 parts (20 on the bottom side), 109 nets.

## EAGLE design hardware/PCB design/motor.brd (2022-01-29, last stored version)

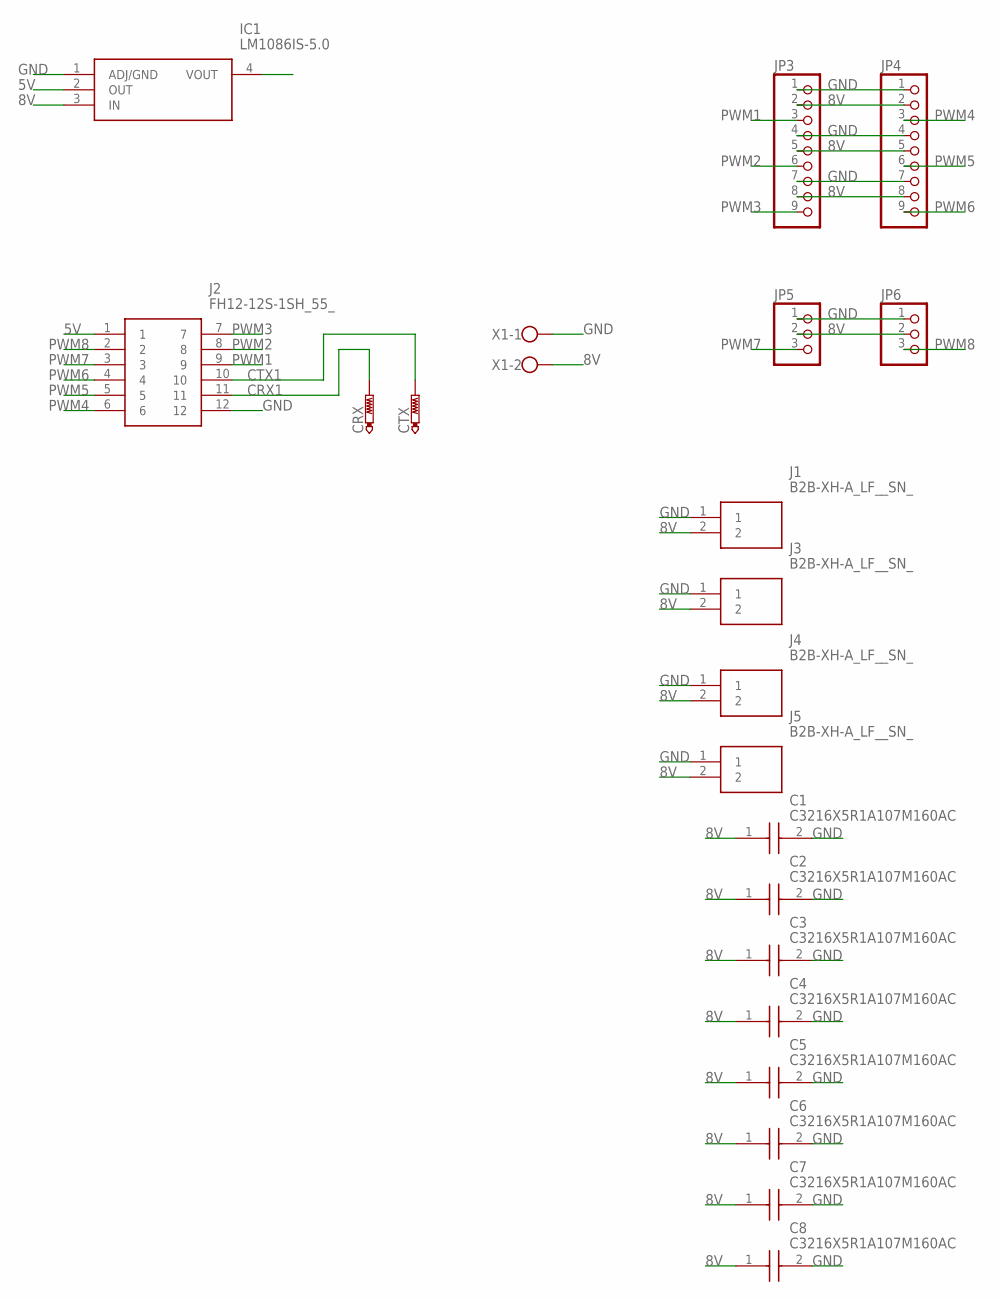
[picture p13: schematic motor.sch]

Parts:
C1, C2, C3, C4, C5, C6, C7, C8: C3216X5R1A107M160AC; CAPC3216X180N
CRX: PTR1TP20R; TP20R
CTX: PTR1TP20SQ; TP20SQ
IC1: LM1086IS-5.0; TO254P1435X457-4N
J1, J3, J4, J5: B2B-XH-A_LF__SN_; SHDR2W64P0X250_1X2_740X575X700
J2: FH12-12S-1SH_55_; FH12-12S-1SH(55)
JP3, JP4: PINHD-1X9; 1X09
JP5, JP6: PINHD-1X3; 1X03
X1: W237-102

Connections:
5V: IC1.2 (OUT), J2.1
8V: C1.1, C2.1, C3.1, C4.1, C5.1, C6.1, C7.1, C8.1, IC1.3 (IN), J1.2, J3.2, J4.2, J5.2, JP3.2, JP3.5, JP3.8, JP4.2, JP4.5, JP4.8, JP5.2, JP6.2, X1.2
CRX1: CRX.TP, J2.11
CTX1: CTX.TP, J2.10
GND: C1.2, C2.2, C3.2, C4.2, C5.2, C6.2, C7.2, C8.2, IC1.1 (ADJ/GND), J1.1, J2.12, J3.1, J4.1, J5.1, JP3.1, JP3.4, JP3.7, JP4.1, JP4.4, JP4.7, JP5.1, JP6.1, X1.1
PWM1: J2.9, JP3.3
PWM2: J2.8, JP3.6
PWM3: J2.7, JP3.9
PWM4: J2.6, JP4.3
PWM5: J2.5, JP4.6
PWM6: J2.4, JP4.9
PWM7: J2.3, JP5.3
PWM8: J2.2, JP6.3

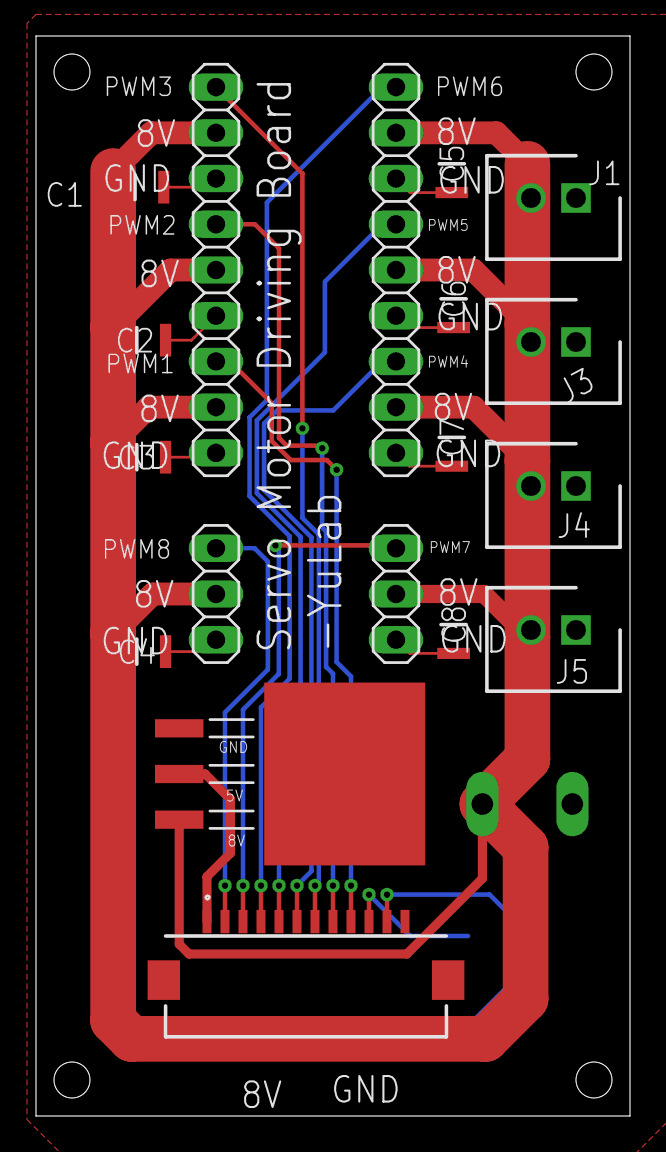
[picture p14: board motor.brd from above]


Board: 2 copper layers, 33.0 x 60.0 mm, 21 parts (3 on the bottom side), 13 nets.

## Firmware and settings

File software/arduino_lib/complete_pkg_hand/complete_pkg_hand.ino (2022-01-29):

//sending data by CAN BUS
//#include <Servo.h>
//int servoPin = 9;
//Servo Servo1;
String readString;
int pos_1;
const PROGMEM int pos_1_roof = 160;
const PROGMEM int pos_1_floor = 1;
int pos_2;
const PROGMEM int pos_2_roof = 100;
const PROGMEM int pos_2_floor = 180;
int pos_3;
const PROGMEM int pos_3_roof = 180;
const PROGMEM int pos_3_floor = 15;
int pos_4;
const PROGMEM int pos_4_roof = 1;
const PROGMEM int pos_4_floor = 180;
int pos_5;
const PROGMEM int pos_5_roof = 180;
const PROGMEM int pos_5_floor = 15;
int pos_6;
const PROGMEM int pos_6_roof = 180;
const PROGMEM int pos_6_floor = 5;

#include <Servo.h>
Servo myservo_1;  // create servo object to control a servo
Servo myservo_2;  // create servo object to control a servo
Servo myservo_3;  // create servo object to control a servo
Servo myservo_4;  // create servo object to control a servo
Servo myservo_5;  // create servo object to control a servo
Servo myservo_6;  // create servo object to control a servo

// name init-final 20210515
#define Servo_1 8 //thumb flexion  8-
#define Servo_2 12 //thumb abduction  12+
#define Servo_3 6 //midlle 6+
#define Servo_4 7 //index 7+
#define Servo_5 10 //little 10+
#define Servo_6 9 //ring 9-


#include <CD74HC4067.h>
CD74HC4067 my_mux(0, 1, 2, 3);
#define S3 3
#define S2 2
#define S1 1
#define S0 0

#define NUM_Data 292
#define NUM_MAG 45
#define NUM_RES 240 //piezoresistive sensing

int x = 0;

#include <Wire.h>
#include <MLX90393.h> //From https://github.com/tedyapo/arduino-MLX90393 by Theodore Yapo

MLX90393 mlx;
MLX90393::txyz data; //Create a structure, called data, of four floats (t, x, y, and z)

MLX90393 mlx_2;
MLX90393::txyz data_2; //Create a structure, called data, of four floats (t, x, y, and z)

MLX90393 mlx_3;
MLX90393::txyz data_3; //Create a structure, called data, of four floats (t, x, y, and z)

#define TCAADDR 0x70
#define bus1 0
#define bus2 1
#define bus3 2
#define bus4 3
#define bus5 4


#define delay_n (uint8_t)1

#define A_0 4
#define B_0 5

int8_t n = 0; //starting from 0 can make the equavalent number for each column reading
uint8_t col;
uint8_t col_ind;
int16_t mag_x;
int16_t mag_y;
int16_t mag_z;
int8_t temp;
int16_t mag_x_2;
int16_t mag_y_2;
int16_t mag_z_2;
int8_t temp_2;
int16_t mag_x_3;
int16_t mag_y_3;
int16_t mag_z_3;
int16_t temp_3;

int16_t data_to_send[NUM_Data];
unsigned long previousTime = micros();
unsigned long timeIntervalData = 5000;// micro seconds, wait to send data
bool SENT = false;
bool TO_GRASP = true;

void setup() {
  // put your setup code here, to run once:
  Serial.begin(115200);
  //  Serial.setTimeout(50);
  delay(100);
  // set up mlx90393
  Wire.begin();
  Wire.setClock(1000000); //at least faster than 1000000, 1000000 is too fast to get correct signal of only two fingers.
  //  //Connect to sensor with I2C address jumpers set: A1 = 1, A0 = 0
  //  //Use DRDY pin connected to A3
  //  //Returns byte containing status bytes
  delay(500);
  activate_finger(bus1);
  activate_finger(bus2);
  activate_finger(bus3);
  activate_finger(bus4);
  activate_finger(bus5);

  delay(100);
  pinMode(A0, INPUT);
  pinMode(A1, INPUT);
  pinMode(A2, INPUT);
  pinMode(A3, INPUT);

  pinMode(S0, OUTPUT);  // sets the pin as output
  pinMode(S1, OUTPUT);  // sets the pin as output
  pinMode(S2, OUTPUT);  // sets the pin as output
  pinMode(S3, OUTPUT);  // sets the pin as output

  delay(100);

  myservo_1.attach(Servo_1);  //the pin for the servo control
  myservo_2.attach(Servo_2);  //the pin for the servo control
  myservo_3.attach(Servo_3);  //the pin for the servo control
  myservo_4.attach(Servo_4);  //the pin for the servo control
  myservo_5.attach(Servo_5);  //the pin for the servo control
  myservo_6.attach(Servo_6);  //the pin for the servo control
  init_motor();// move fingers to initial position
  delay(100);
}

void loop() {
  //  x++;
  //  Servo1.write(x / 90);
  // put your main code here, to run repeatedly:
  //  unsigned long currentMillis = millis();
  unsigned long start = micros();
  if (SENT == true) {
    read_all_data();
    unsigned long end = micros();
    unsigned long delta = end - start;
    data_to_send[285] = myservo_1.read();
    data_to_send[286] = myservo_2.read();
    data_to_send[287] = myservo_3.read();
    data_to_send[288] = myservo_4.read();
    data_to_send[289] = myservo_5.read();
    data_to_send[290] = myservo_6.read();
    
    data_to_send[NUM_Data - 1] = 1000000 / delta;
    SENT = false;
  }

  // wait for sending data
  unsigned long currentTime = micros();
  if (currentTime - previousTime > timeIntervalData) {
    previousTime = currentTime;
    //print data
    print_data(data_to_send, NUM_Data);
//    send_data(data_to_send, NUM_Data);
//    print_all_data(data_to_send);
    SENT = true;
  }
  // receive motor command and execute
  move_fingers2();
}

void print_data(int16_t data_to_send[NUM_Data], int16_t NUM_Data_print) {
//  Serial.print('Data Length:'); //start flag
//  Serial.print(NUM_Data_print);
//  Serial.println(': ');
  for (int i = 0; i < NUM_Data_print; i = i + 1) {
    if (i == NUM_Data_print - 1) {
      Serial.println(data_to_send[i]);
    }
    else {
      Serial.print(data_to_send[i]);
      Serial.print(' ');
    }
  }
  delayMicroseconds(100);
}

void move_fingers() {
  while (Serial.available()) {
    char c = Serial.read();  //gets one byte from serial buffer
    readString += c; //makes the string readString
    delay(2);  //slow looping to allow buffer to fill with next character
  }
  if (readString.length() > 0) {
    String motor = readString[0];
    int n = motor.toInt();  //convert readString into a number
    Serial.print("motor:");
    Serial.println(n);  //so you can see the captured string
    //  Serial.println("initiate position");
    //  pinch(n);
    String deg = "";
    for (int i = 1; i < sizeof(readString); i++) {
      String d = readString[i];
      deg = deg + d;
    }
    int degree = deg.toInt();
    Serial.print("degree to move:");
    Serial.println(degree);
    readString = ""; //empty for next input
    if (n == 0) {
      init_motor();
    }
    if (n == 1) {
      int dest = myservo_1.read() - degree;
      if (dest > pos_1_roof && dest < pos_1_floor) {
        myservo_1.write(dest);
        Serial.print("current degree:");
        Serial.println(myservo_1.read());
      }
      else {
        Serial.println("unable to move, out of range");
        Serial.print("current degree:");
        Serial.println(myservo_1.read());
      }
    }
    if (n == 2) {
      int dest = myservo_2.read() - degree;
      if (dest > pos_2_roof && dest < pos_2_floor) {
        myservo_2.write(dest);
        Serial.print("current degree:");
        Serial.println(myservo_2.read());
      }
      else {
        Serial.println("unable to move, out of range");
        Serial.print("current degree:");
        Serial.println(myservo_2.read());
      }
    }
    if (n == 3) {
      int dest = myservo_3.read() + degree;
      if (dest < pos_3_roof && dest > pos_3_floor) {
        myservo_3.write(dest);
        Serial.print("current degree:");
        Serial.println(myservo_3.read());
      }
      else {
        Serial.println("unable to move, out of range");
        Serial.print("current degree:");
        Serial.println(myservo_3.read());
      }
    }
    if (n == 4) {
      int dest = myservo_4.read() - degree;
      if (dest > pos_4_roof && dest < pos_4_floor) {
        myservo_4.write(dest);
        Serial.print("current degree:");
        Serial.println(myservo_4.read());
      }
      else {
        Serial.println("unable to move, out of range");
        Serial.print("current degree:");
        Serial.println(myservo_4.read());
      }
    }
    if (n == 5) {
      int dest = myservo_5.read() + degree;
      if (dest < pos_5_roof && dest > pos_5_floor) {
        myservo_5.write(dest);
        Serial.print("current degree:");
        Serial.println(myservo_5.read());
      }
      else {
        Serial.println("unable to move, out of range");
        Serial.print("current degree:");
        Serial.println(myservo_5.read());
      }
    }
    if (n == 6) {
      int dest = myservo_6.read() + degree;
      if (dest < pos_6_roof && dest > pos_6_floor) {
        myservo_6.write(dest);
        Serial.print("current degree:");
        Serial.println(myservo_6.read());
      }
      else {
        Serial.println("unable to move, out of range");
        Serial.print("current degree:");
        Serial.println(myservo_6.read());
      }
    }
  }
}

void move_fingers2() {
  // send motor command by "<m1deg1><m2deg2>..."
  bool START_MT = false;
  bool START_DEG = false;
  while (Serial.available()) {
    char c = Serial.read();  //gets one byte from serial buffer
    //    delay(1);
    if (c == '<') {
      START_MT = true;
//      Serial.println("start to read motor");
    }
    if (START_MT == true) {
      char m = Serial.read();
      String motor = m;
      //      delay(1);
      int n = motor.toInt();
//      Serial.print("motor:");
//      Serial.println(n);  //so you can see the captured string
      START_MT = false;
      START_DEG = true;

      String deg = "";
      while (Serial.available() and START_DEG == true) {
        char d = Serial.read();
        //        delay(1);
        if (d == '>') {

          START_DEG = false;
          continue;
        }
        deg += d;
      }
      int degree = deg.toInt();

//      Serial.print("degree:");
//      Serial.println(degree);  //so you can see the captured string
      if (n == 0) {
        init_motor();
      }
      if (n == 1) {
        int dest = myservo_1.read() + degree;
        if (dest <= pos_1_roof && dest >= pos_1_floor) {
          myservo_1.write(dest);
//          Serial.print("current degree:");
//          Serial.println(myservo_1.read());
        }
        else {
//          Serial.println("unable to move, out of range");
//          Serial.print("current degree:");
//          Serial.println(myservo_1.read());
        }
      }
      if (n == 2) {
        int dest = myservo_2.read() - degree;
        if (dest >= pos_2_roof && dest <= pos_2_floor) {
          myservo_2.write(dest);
//          Serial.print("current degree:");
//          Serial.println(myservo_2.read());
        }
        else {
//          Serial.println("unable to move, out of range");
//          Serial.print("current degree:");
//          Serial.println(myservo_2.read());
        }
      }
      if (n == 3) {
        int dest = myservo_3.read() + degree;
        if (dest <= pos_3_roof && dest >= pos_3_floor) {
          myservo_3.write(dest);
//          Serial.print("current degree:");
//          Serial.println(myservo_3.read());
        }
        else {
//          Serial.println("unable to move, out of range");
//          Serial.print("current degree:");
//          Serial.println(myservo_3.read());
        }
      }
      if (n == 4) {
        int dest = myservo_4.read() - degree;
        if (dest >= pos_4_roof && dest <= pos_4_floor) {
          myservo_4.write(dest);
//          Serial.print("current degree:");
//          Serial.println(myservo_4.read());
        }
        else {
//          Serial.println("unable to move, out of range");
//          Serial.print("current degree:");
//          Serial.println(myservo_4.read());
        }
      }
      if (n == 5) {
        int dest = myservo_5.read() + degree;
        if (dest <= pos_5_roof && dest >= pos_5_floor) {
          myservo_5.write(dest);
//          Serial.print("current degree:");
//          Serial.println(myservo_5.read());
        }
        else {
//          Serial.println("unable to move, out of range");
//          Serial.print("current degree:");
//          Serial.println(myservo_5.read());
        }
      }
      if (n == 6) {
        int dest = myservo_6.read() + degree;
        if (dest <= pos_6_roof && dest >= pos_6_floor) {
          myservo_6.write(dest);
//          Serial.print("current degree:");
//          Serial.println(myservo_6.read());
        }
        else {
//          Serial.println("unable to move, out of range");
//          Serial.print("current degree:");
//          Serial.println(myservo_6.read());
        }
      }
    }
    //    delay(2);  //slow looping to allow buffer to fill with next character
  }
}

void send_data(int16_t data_to_send[NUM_Data], int16_t NUM_Data_print) {
  Serial.write('<'); //start flag
  Serial.write(0x00);
  for (int i = 0; i < NUM_Data_print; i = i + 1) {
    if (i == NUM_Data_print - 1) {
      Serial.write(highByte(data_to_send[i]));
      Serial.write(lowByte(data_to_send[i]));
      Serial.write('>');
    }
    else {
      Serial.write(highByte(data_to_send[i]));
      Serial.write(lowByte(data_to_send[i]));
    }
  }
  delayMicroseconds(100);
}

void init_motor() {
//  Serial.println("initiate position");
  myservo_1.write(pos_1_floor);
  myservo_2.write(pos_2_floor);
  myservo_3.write(pos_3_floor);
  myservo_4.write(pos_4_floor);
  myservo_5.write(pos_5_floor);
  myservo_6.write(pos_6_floor);
}

void pinch_2() {
//  Serial.println("initiate position");
  myservo_1.write(pos_1_floor);
  myservo_2.write(80);
  myservo_3.write(pos_3_floor);
  myservo_4.write(70);
  myservo_5.write(pos_5_floor);
  myservo_6.write(pos_6_floor);
}

void move_thumb_flexion(int8_t deg) {
  int s2_dest = myservo_2.read() - deg;
  if (s2_dest < pos_2_roof) {
    myservo_2.write(pos_2_roof);
  }
  else {
    myservo_2.write(s2_dest);
  }
}

void move_thumb_abd(int8_t deg) {
  int s1_dest = myservo_1.read() - deg;
  if (s1_dest < pos_1_roof) {
    myservo_1.write(pos_1_roof);
  }
  else if (s1_dest > pos_1_floor) {
    myservo_1.write(pos_1_floor);
  }
  else {
    myservo_1.write(s1_dest);
  }
}

void move_index(int8_t deg) {
  int s4_dest = myservo_4.read() - deg;
  if (s4_dest < pos_4_roof) {
    myservo_4.write(pos_4_roof);
  }
  else if (s4_dest > pos_4_floor) {
    myservo_4.write(pos_4_floor);
  }
  else {
    myservo_4.write(s4_dest);
  }
}

void move_mid(int8_t deg) {
  int s3_dest = myservo_3.read() + deg;
  if (s3_dest > pos_3_roof) {
    myservo_3.write(pos_3_roof);
  }
  else if (s3_dest < pos_3_floor) {
    myservo_3.write(pos_3_floor);
  }
  else {
    myservo_3.write(s3_dest);
  }
}

void move_ring(int8_t deg) {
  int s6_dest = myservo_6.read() + deg;
  if (s6_dest > pos_6_roof) {
    myservo_6.write(pos_6_roof);
  }
  else if (s6_dest < pos_6_floor) {
    myservo_6.write(pos_6_floor);
  }
  else {
    myservo_6.write(s6_dest);
  }
}

void move_little(int8_t deg) {
  int s5_dest = myservo_5.read() + deg;
  if (s5_dest > pos_5_roof) {
    myservo_5.write(pos_5_roof);
  }
  else if (s5_dest < pos_5_floor) {
    myservo_5.write(pos_5_floor);
  }
  else {
    myservo_5.write(s5_dest);
  }
}

void pinch(int8_t deg) {
  move_thumb_flexion(deg * 0.5);
  //  move_thumb_abd(deg*0.5);
  move_index(deg);
  //  move_mid(deg);
  //  move_ring(deg);
  //  move_little(deg);
}

void print_all_data(int16_t data_to_send[NUM_Data]) {
  ////print data
  for (byte i = 0; i < NUM_Data; i = i + 1) {
    if (i == NUM_Data - 1) {
      Serial.println(data_to_send[i]);
    }
    else {
      Serial.print(data_to_send[i]);
      Serial.print(' ');
    }
  }
}

void read_all_data() {

  for (uint8_t col = 0; col < 12; col++) {

    //Matrix data
    switch (col) {
      case 0:
        digital_write_COL1();
        n++;
        break;
      case 1:
        digital_write_COL2();
        n++;
        break;
      case 2:
        digital_write_COL3();
        n++;
        break;
      case 3:
        digital_write_COL4();
        n++;
        break;
      case 4:
        digital_write_COL5();
        n++;
        break;
      case 5:
        digital_write_COL6();
        n++;
        break;
      case 6:
        digital_write_COL7();
        n++;
        break;
      case 7:
        digital_write_COL8();
        n++;
        break;
      case 8:
        digital_write_COL9();
        n++;
        break;
      case 9:
        digital_write_COL10();
        n++;
        break;
      case 10:
        digital_write_COL11();
        n++;
        break;
      case 11:
        digital_write_COL12();
        n++;
        break;
    }

    read_resistive_data(&data_to_send[45 + 20 * col], &data_to_send[45 + 20 * col + 1], &data_to_send[45 + 20 * col + 2], &data_to_send[45 + 20 * col + 3],
                        &data_to_send[45 + 20 * col + 4], &data_to_send[45 + 20 * col + 5], &data_to_send[45 + 20 * col + 6], &data_to_send[45 + 20 * col + 7],
                        &data_to_send[45 + 20 * col + 8], &data_to_send[45 + 20 * col + 9], &data_to_send[45 + 20 * col + 10], &data_to_send[45 + 20 * col + 11],
                        &data_to_send[45 + 20 * col + 12], &data_to_send[45 + 20 * col + 13], &data_to_send[45 + 20 * col + 14], &data_to_send[45 + 20 * col + 15],
                        &data_to_send[45 + 20 * col + 16], &data_to_send[45 + 20 * col + 17], &data_to_send[45 + 20 * col + 18], &data_to_send[45 + 20 * col + 19]);

    //I2C data
    if (col == 11) {
      read_mag_finger(bus1, &data_to_send[0], &data_to_send[1], &data_to_send[2],
                      &data_to_send[3], &data_to_send[4], &data_to_send[5],
                      &data_to_send[6], &data_to_send[7], &data_to_send[8]);
      read_mag_finger(bus2, &data_to_send[9], &data_to_send[10], &data_to_send[11],
                      &data_to_send[12], &data_to_send[13], &data_to_send[14],
                      &data_to_send[15], &data_to_send[16], &data_to_send[17]);
      read_mag_finger(bus3, &data_to_send[18], &data_to_send[19], &data_to_send[20],
                      &data_to_send[21], &data_to_send[22], &data_to_send[23],
                      &data_to_send[24], &data_to_send[25], &data_to_send[26]);
      read_mag_finger(bus4, &data_to_send[27], &data_to_send[28], &data_to_send[29],
                      &data_to_send[30], &data_to_send[31], &data_to_send[32],
                      &data_to_send[33], &data_to_send[34], &data_to_send[35]);
      read_mag_finger(bus5, &data_to_send[36], &data_to_send[37], &data_to_send[38],
                      &data_to_send[39], &data_to_send[40], &data_to_send[41],
                      &data_to_send[42], &data_to_send[43], &data_to_send[44]);
    }
  }
}

void switch_SP4T(byte B_bool, byte A_bool) {
  digitalWrite(A_0, A_bool);
  digitalWrite(B_0, B_bool);
}

void read_resistive_data(int16_t* mat1, int16_t* mat2, int16_t* mat3, int16_t* mat4,
                         int16_t* mat5, int16_t* mat6, int16_t* mat7, int16_t* mat8,
                         int16_t* mat9, int16_t* mat10, int16_t* mat11, int16_t* mat12,
                         int16_t* mat13, int16_t* mat14, int16_t* mat15, int16_t* mat16,
                         int16_t* mat17, int16_t* mat18, int16_t* mat19, int16_t* mat20)
{
  switch_SP4T(LOW, LOW);
  *mat1 = analogRead(A0);
  *mat5 = analogRead(A1);
  *mat9 = analogRead(A2);
  *mat13 = analogRead(A3);
  *mat17 = analogRead(A6);

  switch_SP4T(LOW, HIGH);
  *mat2 = analogRead(A0);
  *mat6 = analogRead(A1);
  *mat10 = analogRead(A2);
  *mat14 = analogRead(A3);
  *mat18 = analogRead(A6);

  switch_SP4T(HIGH, LOW);
  *mat3 = analogRead(A0);
  *mat7 = analogRead(A1);
  *mat11 = analogRead(A2);
  *mat15 = analogRead(A3);
  *mat19 = analogRead(A6);

  switch_SP4T(HIGH, HIGH);
  *mat4 = analogRead(A0);
  *mat8 = analogRead(A1);
  *mat12 = analogRead(A2);
  *mat16 = analogRead(A3);
  *mat20 = analogRead(A6);

  //  int ROW_1 = analogRead(A0);  // read the input pin 0-1023
  //  int ROW_2 = analogRead(A1);  // read the input pin
  //  int ROW_3 = analogRead(A2);  // read the input pin
  //  int ROW_4 = analogRead(A3);  // read the input pin

  //  int read_digital1 = analogRead(A6);
  //  int read_digital2 = analogRead(A7);
  //  int read_digital3 = analogRead(A8);
  //  int read_digital4 = analogRead(A9);

  //  Serial.print(col);      // debug value
  //  Serial.print(" ");
  //  Serial.print(ROW_1_0);          // debug value
  //  Serial.print(" ");
  //  Serial.print(ROW_2_0);          // debug value
  //  Serial.print(" ");
  //  Serial.print(ROW_3_0);          // debug value
  //  Serial.print(" ");
  //  Serial.print(ROW_4_0);           // debug value
  //  Serial.print(" ");
  //  Serial.print(ROW_1_1);          // debug value
  //  Serial.print(" ");
  //  Serial.print(ROW_2_1);          // debug value
  //  Serial.print(" ");
  //  Serial.print(ROW_3_1);          // debug value
  //  Serial.print(" ");
  //  Serial.print(ROW_4_1);           // debug value
  //  Serial.print(" ");
  //  return;
}

void tcaselect(byte i) {
  if (i > 7) return;
  Wire.beginTransmission(TCAADDR);
  Wire.write(1 << i);
  Wire.endTransmission();
}

void activate_finger(byte bus) {
  tcaselect(bus);
  byte status_1 = mlx.begin(0, 0);
  delay(200);
  byte status_2 = mlx_2.begin(0, 1);
  delay(200);
  byte status_3 = mlx_3.begin(1, 1);
  delay(200);
  mlx.setGainSel(7);
  mlx.setResolution(0, 0, 0); //x, y, z
  mlx.setOverSampling(0);
  mlx.setDigitalFiltering(0);
  delay(50);

  mlx_2.setGainSel(7);
  mlx_2.setResolution(0, 0, 0); //x, y, z
  mlx_2.setOverSampling(0);
  mlx_2.setDigitalFiltering(0);
  delay(50);

  mlx_3.setGainSel(7);
  mlx_3.setResolution(0, 0, 0); //x, y, z
  mlx_3.setOverSampling(0);
  mlx_3.setDigitalFiltering(0);
  delay(100);
}
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

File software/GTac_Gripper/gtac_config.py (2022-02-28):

# this configuration file is for GTac-Gripper.
import numpy as np
import sklearn

COLUMNS_RAW_FINGER_DATA = ['mag_x1', 'mag_y1', 'mag_z1',
                           'mag_x2', 'mag_y2', 'mag_z2',
                           'mag_x3', 'mag_y3', 'mag_z3',
                           'mag_x4', 'mag_y4', 'mag_z4',
                           'mag_x5', 'mag_y5', 'mag_z5',
                           'mag_x6', 'mag_y6', 'mag_z6',
                           'mag_x7', 'mag_y7', 'mag_z7',
                           'mag_x8', 'mag_y8', 'mag_z8',
                           'mag_x9', 'mag_y9', 'mag_z9',
                           'mag_x10', 'mag_y10', 'mag_z10',
                           'mag_x11', 'mag_y11', 'mag_z11',
                           'mag_x12', 'mag_y12', 'mag_z12',
                           'mag_x13', 'mag_y13', 'mag_z13',
                           'mag_x14', 'mag_y14', 'mag_z14',
                           'mag_x15', 'mag_y15', 'mag_z15',
                           'mat1', 'mat2', 'mat3', 'mat4',
                           'mat5', 'mat6', 'mat7', 'mat8',
                           'mat9', 'mat10', 'mat11', 'mat12',
                           'mat13', 'mat14', 'mat15', 'mat16',
                           'mat17', 'mat18', 'mat19', 'mat20',
                           'mat1', 'mat2', 'mat3', 'mat4',
                           'mat5', 'mat6', 'mat7', 'mat8',
                           'mat9', 'mat10', 'mat11', 'mat12',
                           'mat13', 'mat14', 'mat15', 'mat16',
                           'mat17', 'mat18', 'mat19', 'mat20',
                           'mat1', 'mat2', 'mat3', 'mat4',
                           'mat5', 'mat6', 'mat7', 'mat8',
                           'mat9', 'mat10', 'mat11', 'mat12',
                           'mat13', 'mat14', 'mat15', 'mat16',
                           'mat17', 'mat18', 'mat19', 'mat20',
                           'mat1', 'mat2', 'mat3', 'mat4',
                           'mat5', 'mat6', 'mat7', 'mat8',
                           'mat9', 'mat10', 'mat11', 'mat12',
                           'mat13', 'mat14', 'mat15', 'mat16',
                           'mat17', 'mat18', 'mat19', 'mat20',
                           'mat1', 'mat2', 'mat3', 'mat4',
                           'mat5', 'mat6', 'mat7', 'mat8',
                           'mat9', 'mat10', 'mat11', 'mat12',
                           'mat13', 'mat14', 'mat15', 'mat16',
                           'mat17', 'mat18', 'mat19', 'mat20',
                           'mat1', 'mat2', 'mat3', 'mat4',
                           'mat5', 'mat6', 'mat7', 'mat8',
                           'mat9', 'mat10', 'mat11', 'mat12',
                           'mat13', 'mat14', 'mat15', 'mat16',
                           'mat17', 'mat18', 'mat19', 'mat20',
                           'mat1', 'mat2', 'mat3', 'mat4',
                           'mat5', 'mat6', 'mat7', 'mat8',
                           'mat9', 'mat10', 'mat11', 'mat12',
                           'mat13', 'mat14', 'mat15', 'mat16',
                           'mat17', 'mat18', 'mat19', 'mat20',
                           'mat1', 'mat2', 'mat3', 'mat4',
                           'mat5', 'mat6', 'mat7', 'mat8',
                           'mat9', 'mat10', 'mat11', 'mat12',
                           'mat13', 'mat14', 'mat15', 'mat16',
                           'mat17', 'mat18', 'mat19', 'mat20',
                           'mat1', 'mat2', 'mat3', 'mat4',
                           'mat5', 'mat6', 'mat7', 'mat8',
                           'mat9', 'mat10', 'mat11', 'mat12',
                           'mat13', 'mat14', 'mat15', 'mat16',
                           'mat17', 'mat18', 'mat19', 'mat20',
                           'mat1', 'mat2', 'mat3', 'mat4',
                           'mat5', 'mat6', 'mat7', 'mat8',
                           'mat9', 'mat10', 'mat11', 'mat12',
                           'mat13', 'mat14', 'mat15', 'mat16',
                           'mat17', 'mat18', 'mat19', 'mat20',
                           'mat1', 'mat2', 'mat3', 'mat4',
                           'mat5', 'mat6', 'mat7', 'mat8',
                           'mat9', 'mat10', 'mat11', 'mat12',
                           'mat13', 'mat14', 'mat15', 'mat16',
                           'mat17', 'mat18', 'mat19', 'mat20',
                           'mat1', 'mat2', 'mat3', 'mat4',
                           'mat5', 'mat6', 'mat7', 'mat8',
                           'mat9', 'mat10', 'mat11', 'mat12',
                           'mat13', 'mat14', 'mat15', 'mat16',
                           'mat17', 'mat18', 'mat19', 'mat20',
                           'servo_1', 'servo_2', 'servo_3', 'servo_4', 'servo_5', 'servo_6',
                           'Hz', 'milliseconds']
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

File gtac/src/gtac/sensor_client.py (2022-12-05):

"""The client for a single GTac sensor."""
import logging
import time
import math

import numpy as np

from .serial_reader import GtacSerialReader


logger = logging.getLogger(__name__)


RF_MAT_ROW = np.array([[0, 0, 0, 0], [1, 1, 1, 1], [3, 3, 3, 3], [2, 2, 2, 2]])
RF_MAT_COL = np.array([[2, 3, 1, 0], [2, 3, 1, 0], [2, 3, 1, 0], [2, 3, 1, 0]])

LF_MAT_ROW = np.array([[0, 0, 0, 0], [1, 1, 1, 1], [3, 3, 3, 3], [2, 2, 2, 2]])
LF_MAT_COL = np.array([[0, 1, 3, 2], [0, 1, 3, 2], [0, 1, 3, 2], [0, 1, 3, 2]])

UP_MAT_ROW = np.array([[2, 3, 1, 0], [2, 3, 1, 0], [2, 3, 1, 0], [2, 3, 1, 0]])
UP_MAT_COL = np.array([[2, 2, 2, 2], [3, 3, 3, 3], [1, 1, 1, 1], [0, 0, 0, 0]])

MAT_ORIENT_ROW = np.array(
    [
        [LF_MAT_ROW, LF_MAT_ROW, LF_MAT_ROW],
        [RF_MAT_ROW, LF_MAT_ROW, LF_MAT_ROW],
        [RF_MAT_ROW, RF_MAT_ROW, RF_MAT_ROW],
        [LF_MAT_ROW, LF_MAT_ROW, LF_MAT_ROW],
        [RF_MAT_ROW, LF_MAT_ROW, LF_MAT_ROW],
    ]
)
MAT_ORIENT_COL = np.array(
    [
        [LF_MAT_COL, LF_MAT_COL, LF_MAT_COL],
        [RF_MAT_COL, LF_MAT_COL, LF_MAT_COL],
        [RF_MAT_COL, RF_MAT_COL, RF_MAT_COL],
        [LF_MAT_COL, LF_MAT_COL, LF_MAT_COL],
        [RF_MAT_COL, LF_MAT_COL, LF_MAT_COL],
    ]
)
MAG_NUM = 45
MAT_NUM = 16


def find_FAI_index(finger, sec, r, c):
    # the FAI index exclude the mag data
    # the overall index is "output"+NUM_MAG
    index = (
        sec * 4 * 20
        + finger * 4
        + MAT_ORIENT_COL[finger, sec, r, c] * 20
        + MAT_ORIENT_ROW[finger, sec, r, c]
    )
    return index + MAG_NUM


def find_FAI(data_frame_array, finger, sec, r, c):
    index = find_FAI_index(finger, sec, r, c)
    return data_frame_array[index]


def find_SAII_index(finger, sec):
    tri_index = finger * 9 + (2 - sec) * 3
    return tri_index, tri_index + 1, tri_index + 2


def find_SAII(data_frame_array, finger, sec):
    # print('SAII_data: finger {}, sec {}'.format(finger, sec))
    tri_index = finger * 9 + (2 - sec) * 3
    mag_x = data_frame_array[tri_index]
    mag_y = data_frame_array[tri_index + 1]
    mag_z = data_frame_array[tri_index + 2]
    SAII_scaler = math.sqrt(mag_x * mag_x + mag_y * mag_y + mag_z * mag_z)
    # print('Find_SAII: {} scalar: {}'.format([mag_x, mag_y, mag_z], SAII_scaler))
    return [mag_x, mag_y, mag_z], SAII_scaler


def find_sec_index(finger, sec):
    # Input: finger, sec
    # Output: the GTac index in one finger section, shape >> 19
    sec_index = []
    for i in range(MAT_NUM):  # MAT_NUM -> 16: there 4*4 sensing points on FA-I layer
        r = i // 4
        c = i % 4
        index = find_FAI_index(finger, sec, r, c)
        sec_index.append(index)
    mag_all = find_SAII_index(finger, sec)
    for m in mag_all:
        sec_index.append(m)
    return sec_index


class GtacInterface:
    """The interface for a single GTac sensor.

    Args:
        serial_port_name: Device name. e.g., /dev/ttyACM0 on Linux and COM3 on Windows.
        data_index: Which of the consecutive 19-number data this sensor corresponds to.
        baud_rate: Serial baud rate.
        frequency: Desired frequency. Warning will be emitted if not satisfied.
    """

    def __init__(
        self,
        serial_port_name: str,
        data_index: int = 0,
        baud_rate: int = 115200,
        frequency=100,
    ):
        self._reader = GtacSerialReader(serial_port_name, baud_rate, frequency)
        self._idx = data_index
        self._finger = data_index // 3
        self._sec = data_index % 3

    def start(self):
        self._reader.start()
        t0 = time.time()
        while self._reader.reading is None:
            time.sleep(0.001)
            if time.time() - t0 > 2:
                raise RuntimeError("GTac sensor reading timeout.")

    def stop(self):
        self._reader.stop()

    @property
    def pressures(self):
        indices = find_sec_index(self._finger, self._sec)
        return self._reader.reading[indices[:16]].reshape([4, 4])

    @property
    def forces(self):
        start = self._finger * 9 + (2 - self._sec) * 3
        return self._reader.reading[start : start + 3]

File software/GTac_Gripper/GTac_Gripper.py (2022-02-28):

import argparse
import collections
import copy
import os.path
import pickle
import threading
import time
from queue import Queue
from collections import deque

import numpy as np
import pandas as pd
import pylab as plt
import serial

# from matplotlib import pyplot as plt, image as mpimg
import sklearn
from matplotlib import image as mpimg
from tensorflow import keras

import gtac_config
# from GTac_Data import gtac_data, gtac_data_analysis
import GTac_Data
from data_gen import raw_data_byts_checkout_2
from gtac_config import fname_img
from ur10_robot import main_ur10_thread


class gtac_gripper:
    def __init__(self, SerialPort, init_mt=False, BaudRate=115200, buffer_size=8, init_pos=None, save=False, remarks='test'):
        # init_motor: whether initialize the motors ar the beginning
        # buffer_size: the buffer size of reading data flow. this can reduce the sharpness of response curve.
        self.SerialPort = SerialPort
        self.BaudRate = BaudRate
        self.ser = self.connect_hand(self.SerialPort, self.BaudRate)
        self.init_mt = init_mt
        if init_mt:
            self.init_motors()
            if init_pos:
                self.init_pose(init_pos)
        self.avg = self._init_GTac(DataPoints=300)
        self.motors_init = self.avg[-1 - gtac_config.MOTOR_NUM:-1]
        self.motors_angle = self.motors_init
        self.buffer = deque(maxlen=buffer_size)
        self.contacted_previous_map = np.zeros((gtac_config.FINGER_NUM, gtac_config.SEC_NUM), dtype=bool)
        self.SA_II_ref = np.zeros((gtac_config.MAG_NUM))
        self.dt_list = []  # to save
        self.save = save
        save_path = 'data/case_study/'
        timestr = time.strftime("%Y%m%d_%H%M%S")
        self.filename = save_path + remarks + '_' + \
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

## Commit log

2022-01-29 init the files
    [fingertip_12line_outlined_2.brd, fingertip_12line_outlined_2.sch, fingertip_16line_2.brd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]
2022-02-11 organized the files
    [SNR.csv, egg_gsp_handover_ECS_results.csv, egg_gsp_handover_GTAC.csv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]
2022-02-28 update code of GTac-Gripper
    [cover_egg_test_5000_GTAC_Gripper20220222_165531.csv, palm_touch_apple_caging_3000_GTAC_Gripper20220214_175211.csv, rolling_baseball_0_3000_GTAC_Gripper20220215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]
2022-04-20 update for gtac sensor
    [test_sensor_300_GTAC_Gripper20220420_192331.csv]
2022-04-20 update readme for GTac sensor
2022-04-20 update sensor readme
2022-04-21 update files elect
    [motor.brd, motor.sch, palm.brd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]
2022-12-02 Add initial python package
    [.bumpversion.cfg]
2022-12-05 Add interface for a single sensor

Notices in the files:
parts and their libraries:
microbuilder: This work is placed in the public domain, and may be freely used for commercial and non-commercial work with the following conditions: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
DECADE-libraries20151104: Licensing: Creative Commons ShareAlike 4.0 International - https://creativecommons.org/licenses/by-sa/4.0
